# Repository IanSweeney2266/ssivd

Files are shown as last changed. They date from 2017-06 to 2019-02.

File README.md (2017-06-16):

# Small Scale Intelligent Vehicle Design platform (SSIVD)
Software and hardware documentation for creating an implementation of the Cal Poly SLO small-scale intelligent vehicle design platform

All original work is licensed under the MIT license, and all derivative work is licensed under the appropriate parent license 

If there are any concerns regarding licensing, get in touch and we will attempt to resolve it as soon as possible

#Statement of Disclaimer

Since this project is a result of a class assignment, it has been graded and accepted as fulfillment of the
course requirements. Acceptance does not imply technical accuracy or reliability. Any use of information
in this report is done at the risk of the user. These risks may include catastrophic failure of the device or
infringement of patent or copyright laws. California Polytechnic State University at San Luis Obispo and
its staff cannot be held liable for any use or misuse of the project.

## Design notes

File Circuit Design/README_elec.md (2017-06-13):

This folder contains the Eagle files for the SSIVD motherboard.

See the final design report for the full bill of materials.

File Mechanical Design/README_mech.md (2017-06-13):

This folder contains the solidworks files for the mechanical system of the SSIVD. 

Note that exact geometries of suspension components may vary, and the length of the steering linkage bar may need to be adjusted.

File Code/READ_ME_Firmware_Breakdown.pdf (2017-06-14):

# Firmware Breakdown

There are many files attached to the main Arduino loop, Teensy_Firmware. In this section we will go over which files you need to be aware of and which you can ignore.

IMU: (From a documented Library)

The BNO055 takes up quite a few files. Adafruit_BNO055.cpp, Adafruit_BNO055.h, Adafruit_Sensor.h, imumaths.h, matrix.h, structs.h, quarternion.h, vector.h, BNO.cpp, and BNO.h all have to do with the IMU. If you need to look into how the IMU is handled start with BNO.cpp and BNO.h as these are the files that incorporate all the rest.

Indicator LED: (User made files)

Fault_handler.cpp and fault_handler.h hold the functions we use to initialize and set the on-board LED. There's not too much here, although if you're looking to change the LED color check out our pre-made selection in fault_handler.h.

Throttle/Steering Input and URF Distance Sensor : (User made files)

All handling of the radio receiver's PWM input is handled through input_handler.cpp and input_handler.h. Here you will find the interrupt that catches the starting timestamp of the PWM and the handling of the calculated difference between that and the ending. We limit the throttle input from –500 to 500 and the servo input from –400 to 400. The URF sensor's initializing and polling functions are also handled here.

Servo Output: (User made files)

Sending a PWM pulse to the servo happens through output_handler.cpp and output_handler.h. The useful functions here are initServo and writeServo.

CAN Library: (From a documented Library)

FlexCAN.cpp, FlexCAN.h, and kinetis_flexcan.h provide a CAN library that allowed us to simply call functions to start the Teesny's CAN bus and to read and send the CAN messages. All CAN library support comes from these two files.

Motor Controller Interfacing: (User made files)

Building from the CAN library in FlexCAN.cpp, uLaren_CAN_Driver.cpp and uLaren_CAN_Driver.h have the heavy task of creating all the specific CAN functionality to use the motor controllers. Setting up their network, initializing them, setting the target velocity and much more is found in these files.

Laser Sensor (From a documented Library)

Adafruit_VL53L0X.cpp, Adafruit_VL53L0X.h, and the twenty other files that start with "vl53l0x" all provide support for the VL53L0X Laser Sensor. The only notable files are the Adafruit_VL53L0X.cpp and the Adafruit_VL53L0X.h. The other files support these two.

Main Loop Support (User made files)

As the system is right now, we have one file that supports the main loop, loop.h. This file contains the states the main loop is allowed to cycle through.

1.1.1 Teensy Main Loop Brief

There are two critical things to know that pertain to the main loop file Teensy_Firmware: the state transitions and the global variables used. We'll start with explaining the state transitions.

INITIALIZE_PERIPHERALS

In this state we initialize any sensors we wish to use. The indicator led gets set to white here. Once we're done here we move on to INITIALIZE_CONTROLLERS.

INITIALIZE_CONTROLLERS

This state is used specifically for the Maxon motor controllers. We start by resetting the nodes in case they were previously in a fault state. We continue by initializing the CAN network for every node (motor controller) on the network and going around one by one and initializing them to various modes and settings. The notable settings are changing to Profile Velocity Mode and turning the controller into the Switched-On state. The code in uLaren_CAN_Driver.cpp is well documented for all settings. Once initialized, the code moves on to the WAIT_FOR_ARM state.

WAIT_FOR_ARM

As the name implies, we wait for the user to arm the system and motor controllers by turning and holding the steering as far right as possible. This is indicated on the LED by transitioning to a yellow color. Once armed, we then transition to the LINK_COMMUNICATION state.

LINK_COMMUNICATION

Here we set each motor controller to the Operation Enabled state which is the final state and enables the motors to be "running". In this state the indicator LED becomes red. The initial velocity here is set to '0' which gives the motors holding power. This stage is rather complex and sometimes we need to try to rearm the controller. The code here handles this case and is quite impressive in its robustness. Once all motor controllers are armed, we go to either the RUNNING_NOMINALLY state or RUNNING_SIMULINK state depending on whether the defined variable SIMULINK is set to a '0' or '1' respectively.

RUNNING_NOMINALLY

This stage is where the loop will stay at until we encounter an error. This state starts by checking to see if any CAN messages can be processed. It then attempts to write a new value to the motor controllers if 20 milliseconds have gone by; if it hasn't then it moves on. We then check the voltage level of the motor controllers to regulate the battery level. We decided to set a minimum voltage level of 22V and if this level isn’t met the LED indicator changes to a purple color and shuts down all the motor controllers. In most cases we continue through the state and attempt to write to the servo if 10 milliseconds have gone by. In this state the indicator LED is green.

RUNNING_SIMULINK

This state is very similar to RUNNING_NOMINALLY. The difference is that instead of taking input directly from the radio receiver we send it to Simulink first and use the values that Simulink sends back. To implement this, we had to use the Raspberry Pi/Simulink as the SPI master while the Teensy was the receiver. We used a one-byte opcode to indicate to the Teensy which functionality the Raspberry Pi/Simulink is trying to use. To achieve this setting we incorporated a switch case using the one-byte prefixed opcode. Other than the switch case this state also incorporates all functionality that the RUNNING_NOMINALLY state has. Here the indicator LED is supposed to be cyan but it looks more white in reality.

INDICATE_AND_LOG_ERROR

WAIT_FOR_CLEAR

These states have yet to be implemented. They were developed in the prototype phase and serve as a base for future projects to use.

1.1.2 Teensy’s Pertinent Variables

SIMULINK: The SIMULINK defined variable is used to switch between the RUNNING_NOMINALLY functionality and the RUNNING SIMULINK functionality by writing a '0' or '1' respectively.

MC_VOLTAGE_THRESHOLD: This variable is used to set a minimum limit that the perceived voltage by the motor controllers must not dip below. This value is counted in 0.1V and we recommend not changing its value.

CANbus: The CANbus global variable is the key to all CAN communication. Key functions regarding this variable are specified in FlexCAN.h.

Next_state: This crucial global variable is how we interpret which state we are currently in.

All data and output variables are self-explanatory and are meant to be apparent in their meaning.

Timing variables are used to control how often we exercise certain functionality. As an example, we use the motor's timing variables to write approximately 50 times per second.

PRINT: Located in uLaren_CAN_Driver.h, if set to a '1' many items will be printed in the serial port and is quite helpful for debugging purposes.

SCALE_FACTOR: Be careful with this defined variable as it controls the factor we scale the throttle by. For normal use we advise not going above 2 to maintain similitude. The motors however are capable of going much higher (up to 8 is theoretically possible but is very strongly advised against and could destroy the motors).

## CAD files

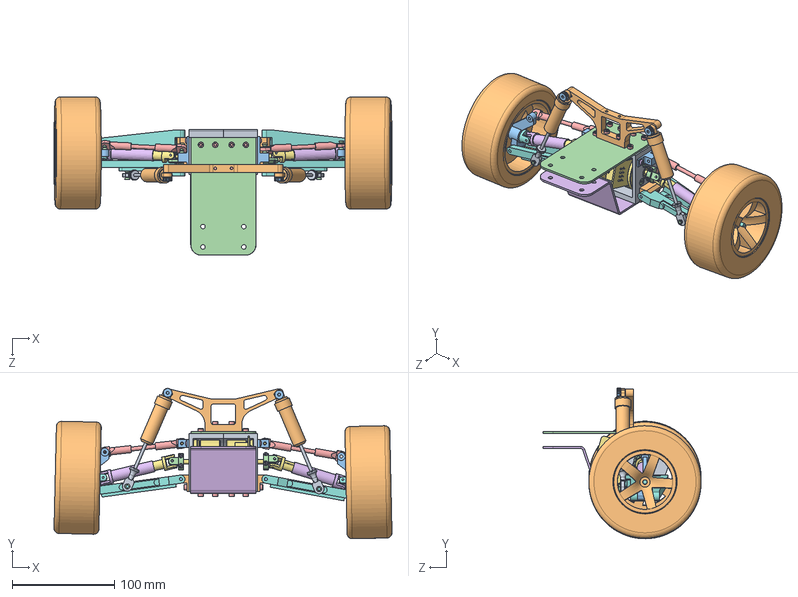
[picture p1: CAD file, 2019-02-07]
Mechanical Design/Parts and Assemblies/Custom Rear.SLDASM
330.9 x 147.4 x 155.0 mm
Rear drivemount_R3
Rear A Pivot x 2
Rear Turnbucklemount x 2
Shaft Coupler - SideA x 2
Shaft Coupler - SideB x 2
M2 - 10MM - Socket x 4
MaxonMotor x 2
U Joint A - Wheel_Rear x 2
U Joint Ball x 4
Wheel x 2
Suspension Mount_Rear x 2
Turnbuckle Ball Spacer x 6
Turnbuckle Bar_REAR x 2
U Joint A - Outer Yoke_Rear x 2
U Joint B - Inner Yoke_Rear x 2
Suspension Plate_R
Suspension Inner_Rear x 2
Suspension Outer_Rear x 2
A-Arm Dowel Pin x 2
M3-4MM -Flat x 6
M3 - 6MM - Socket x 18
M3 - 5MM - Rounded x 4
M3 - 14MM - Rounded x 2
Suspension Plate_L
Rear drivemount_L2
Suspension Mount Rear
M4 - 5MM - Shoulder x 2
Chassis Mount Rear_top
M3 - 12MM - Socket x 2
Chassis Mount RB Sheet Metal

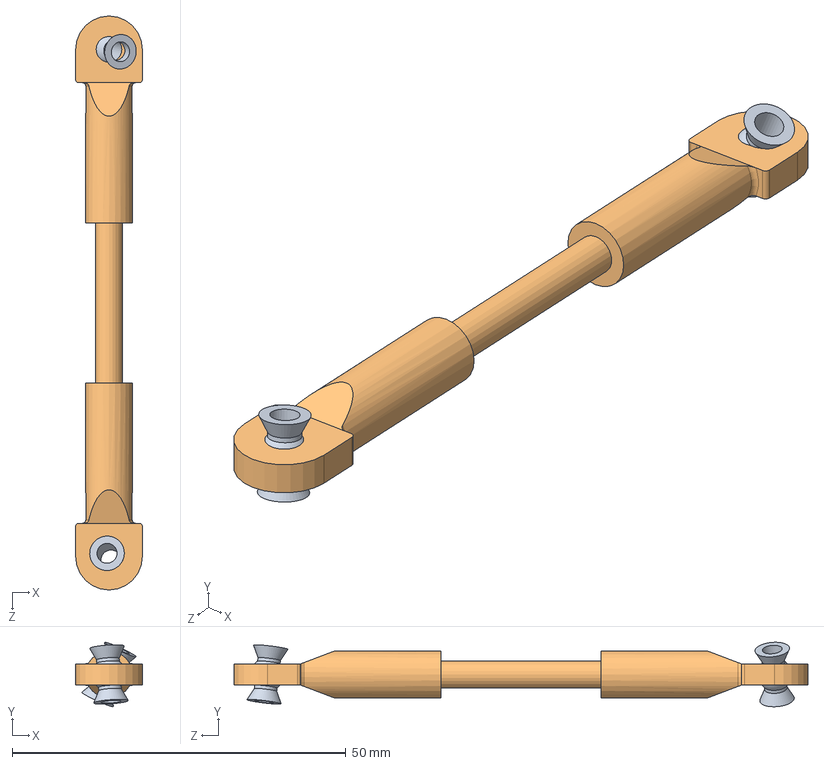
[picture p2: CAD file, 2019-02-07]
Mechanical Design/Parts and Assemblies/Stock Parts/Fore/Steering/Steering TurnbuckleAssy_fore.SLDASM
10.0 x 9.68 x 86.0 mm
Turnbuckle Ball Spacer x 2
Steering turnbuckle Bar_fore

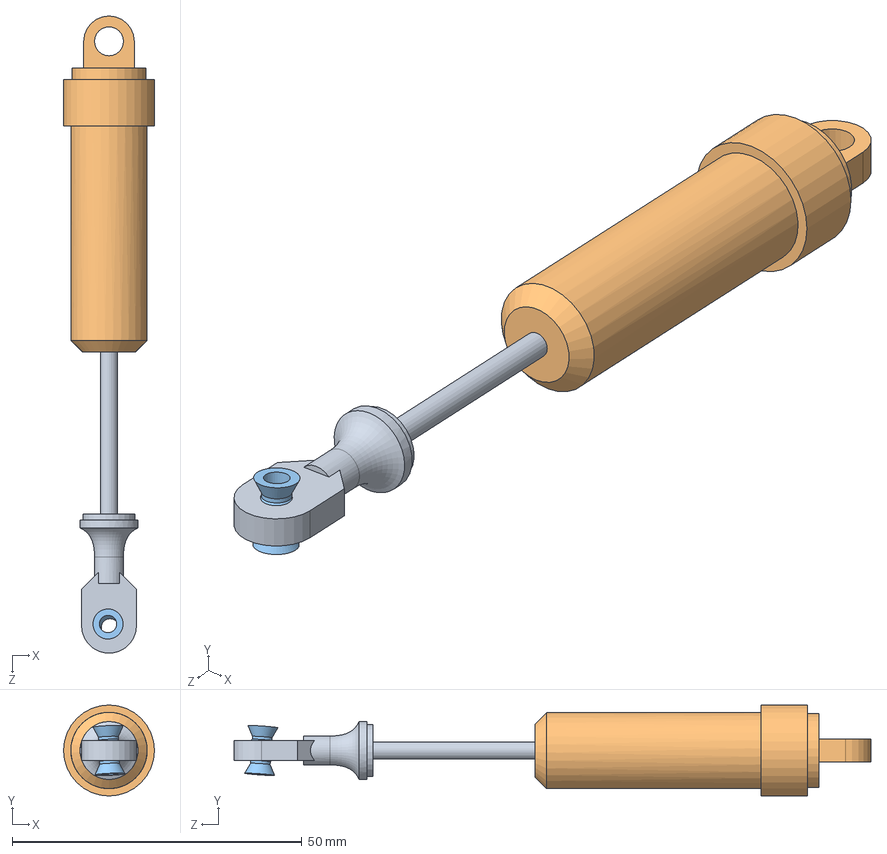
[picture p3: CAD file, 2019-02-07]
Mechanical Design/Parts and Assemblies/Stock Parts/Rear/Suspension_Rear.SLDASM
15.7 x 15.7 x 110.0 mm
Suspension Inner_Rear
Suspension Outer_Rear
Turnbuckle Ball Spacer

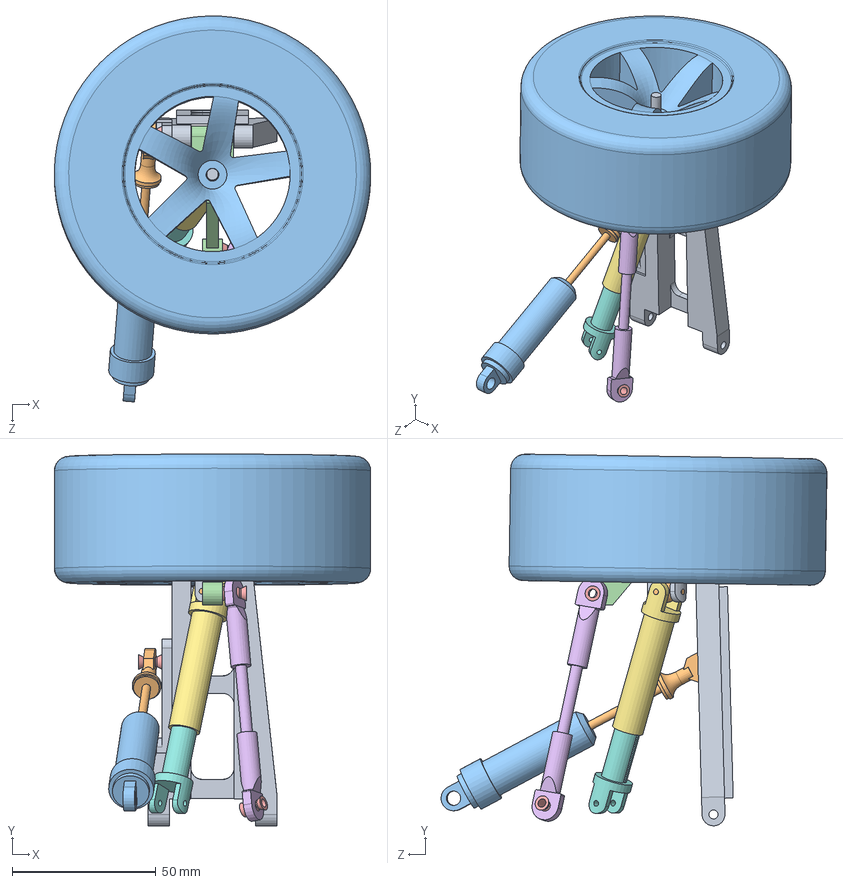
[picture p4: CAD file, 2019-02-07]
Mechanical Design/Parts and Assemblies/Stock Parts/Right Rear Assy.SLDASM
110.0 x 129.2 x 134.2 mm
U Joint A - Wheel_Rear
U Joint Ball
Wheel
Suspension Mount_Rear
Turnbuckle Ball Spacer x 3
Turnbuckle Bar_REAR
U Joint A - Outer Yoke_Rear
U Joint B - Inner Yoke_Rear
Suspension Plate_R
Suspension Inner_Rear
Suspension Outer_Rear

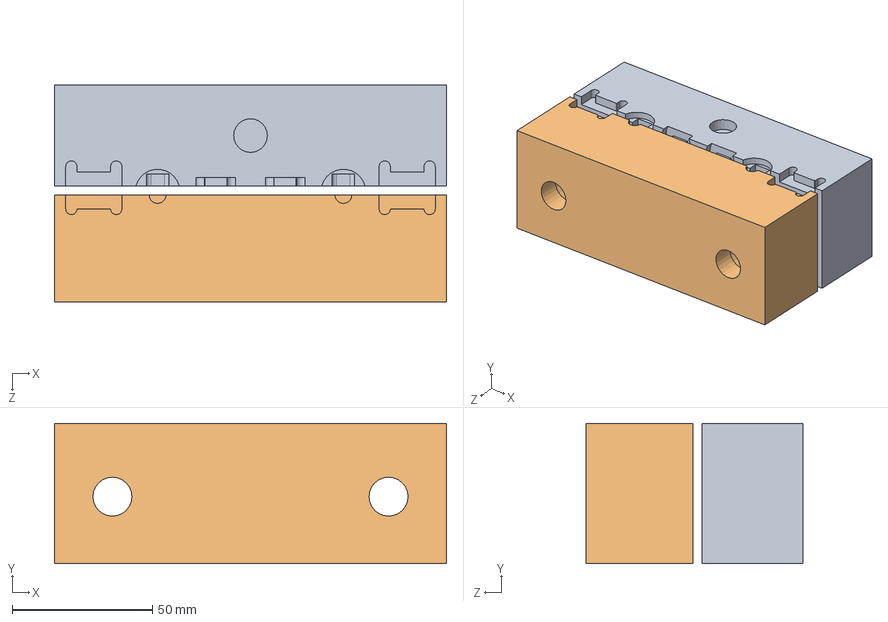
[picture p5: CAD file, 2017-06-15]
Mechanical Design/Automation/cnc/Soft Jaw Cutting Assy.SLDASM
139.7 x 50.0 x 77.3 mm
softjawA
softjawB

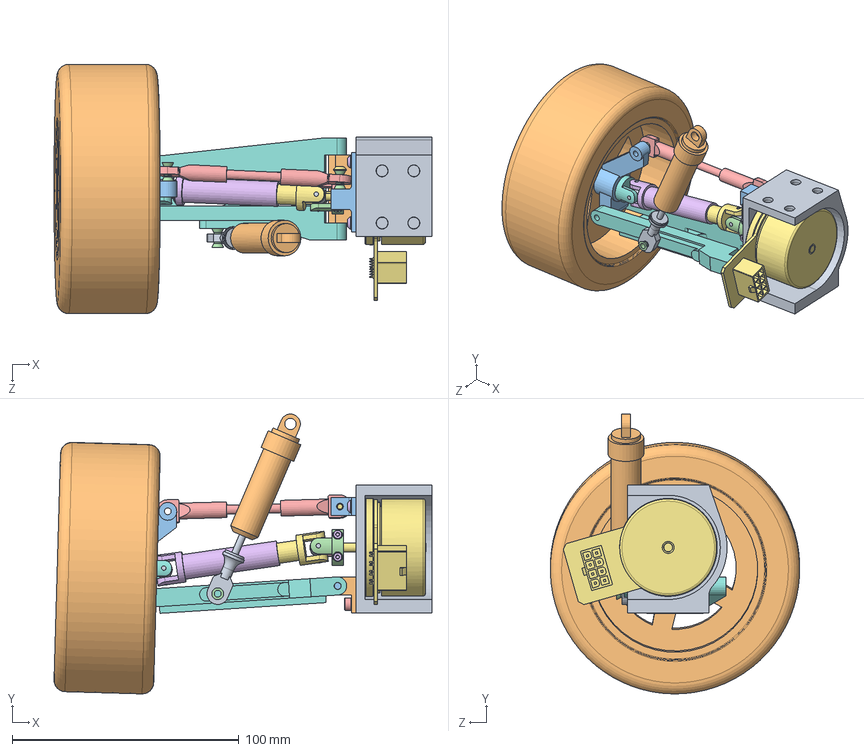
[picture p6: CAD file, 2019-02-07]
Mechanical Design/Parts and Assemblies/Custom Rear_R.SLDASM
166.7 x 123.4 x 109.9 mm
Rear drivemount_R3
Rear A Pivot
Rear Turnbucklemount
Shaft Coupler - SideA
Shaft Coupler - SideB
M2 - 10MM - Socket x 2
MaxonMotor
U Joint A - Wheel_Rear
U Joint Ball x 2
Wheel
Suspension Mount_Rear
Turnbuckle Ball Spacer x 3
Turnbuckle Bar_REAR
U Joint A - Outer Yoke_Rear
U Joint B - Inner Yoke_Rear
Suspension Plate_R
Suspension Inner_Rear
Suspension Outer_Rear
A-Arm Dowel Pin
M3-4MM -Flat x 3
M3 - 6MM - Socket x 2
M3 - 5MM - Rounded x 2
M3 - 14MM - Rounded

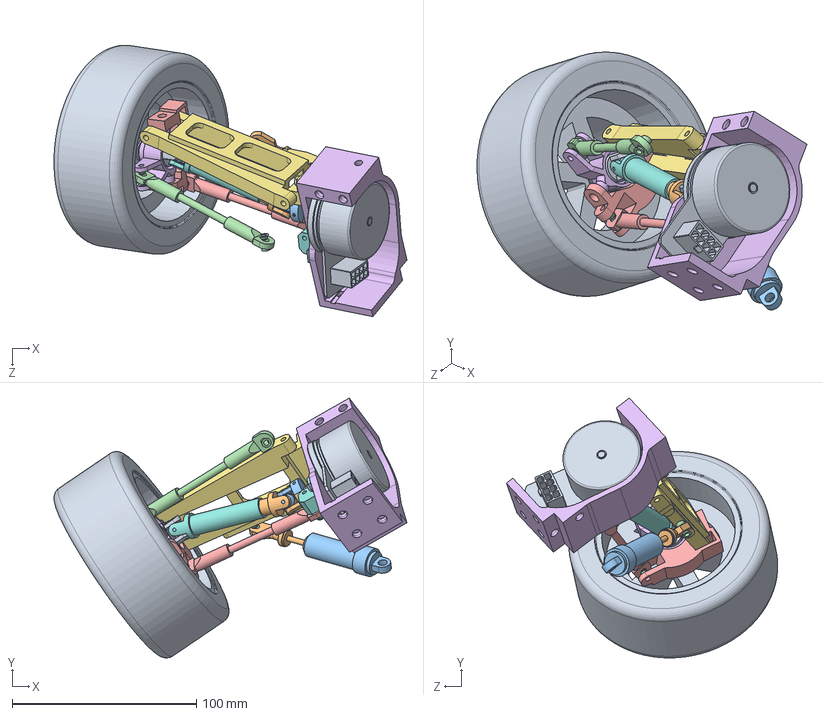
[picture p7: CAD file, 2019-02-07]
Mechanical Design/Parts and Assemblies/Stock Parts/Front Right Assy.SLDASM
191.4 x 140.9 x 147.1 mm
Wheel
Suspension Inner_fore
Suspension Outer_fore
Turnbuckle Ball Spacer x 5
Suspension Mount Fore-Right
SteeringControlArm-Right
Suspension Plate_R
U Joint A - Outer Yoke_fore
U Joint A - Wheel_fore
U Joint B - Inner Yoke_fore
U Joint Ball x 2
Steering turnbuckle Bar_fore
Turnbuckle Bar_fore
Front Drivemount_R2
Front A Pivot
Front Turnbucklemount
MaxonMotor
Shaft Coupler - SideA
Shaft Coupler - SideB
M2 - 10MM - Socket x 2
M3-4MM -Flat x 3
M3 - 5MM - Rounded x 2
M3 - 12MM - Socket x 2
M3 - 14MM - Rounded

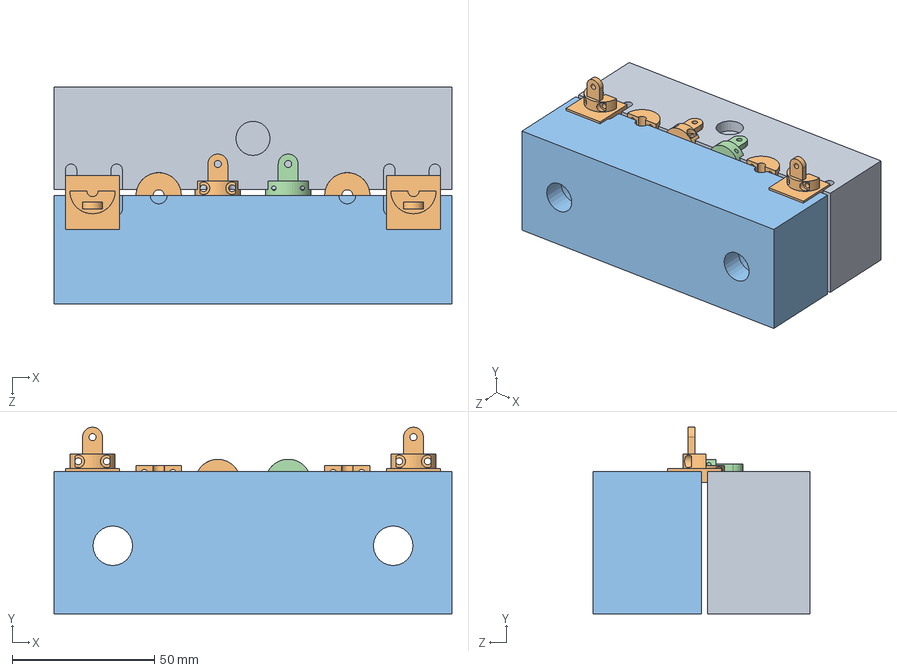
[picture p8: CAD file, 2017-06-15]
Mechanical Design/Automation/cnc/softjawfit.SLDASM
139.7 x 65.5 x 76.1 mm
softjawA
Shaft Coupler - SideA x 5
softjawB
Shaft Coupler - SideB

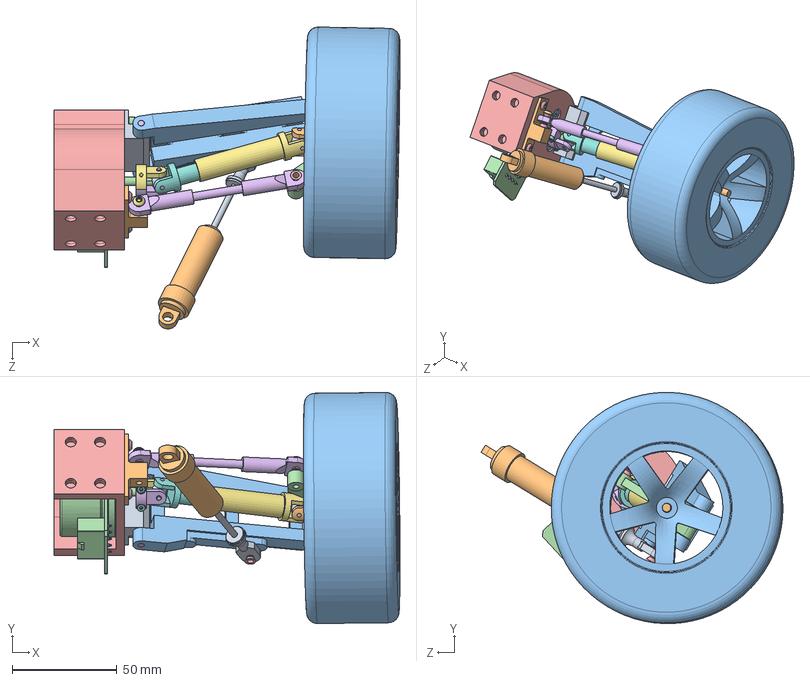
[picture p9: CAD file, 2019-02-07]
Mechanical Design/Parts and Assemblies/Custom Rear_L.SLDASM
165.1 x 110.3 x 144.1 mm
U Joint Ball x 2
U Joint A - Wheel_Rear
Wheel
Suspension Mount_Rear
Turnbuckle Ball Spacer x 3
Turnbuckle Bar_REAR
U Joint A - Outer Yoke_Rear
U Joint B - Inner Yoke_Rear
Suspension Inner_Rear
Suspension Outer_Rear
Suspension Plate_L
MaxonMotor
Rear drivemount_L2
Shaft Coupler - SideA
Shaft Coupler - SideB
M2 - 10MM - Socket x 2
Rear A Pivot
Rear Turnbucklemount
M3-4MM -Flat x 3
M3 - 6MM - Socket x 2
M3 - 5MM - Rounded x 2
A-Arm Dowel Pin
M3 - 14MM - Rounded

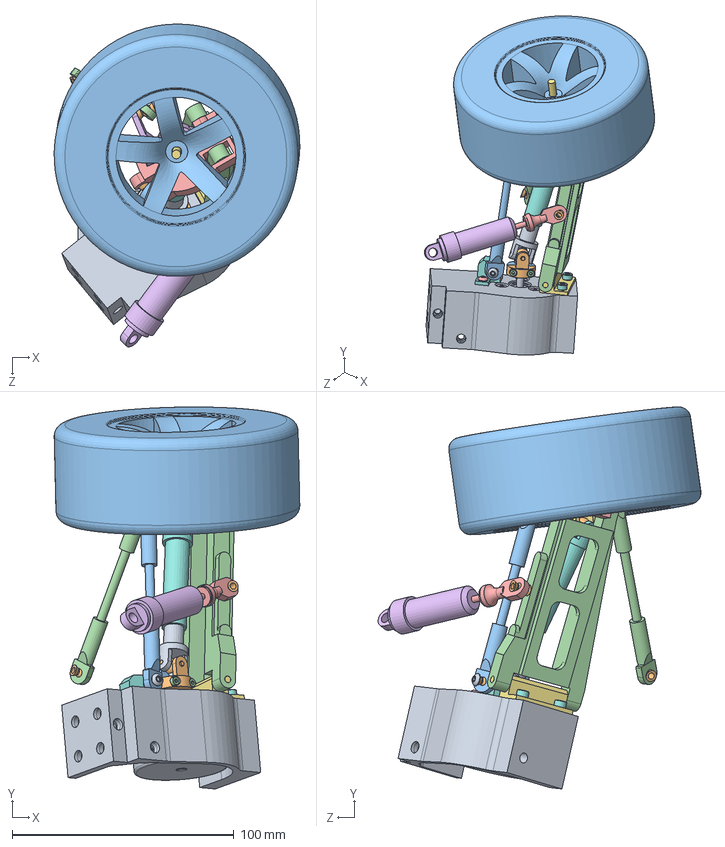
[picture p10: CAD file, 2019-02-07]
Mechanical Design/Parts and Assemblies/Stock Parts/Front Left Assy.SLDASM
110.7 x 172.2 x 145.5 mm
Front Drivemount_L2
U Joint Ball x 2
Wheel
Suspension Plate_L
Suspension Mount Fore-Left
SteeringControlArm-Left
U Joint A - Wheel_fore
U Joint A - Outer Yoke_Rear
U Joint B - Inner Yoke_Rear
Turnbuckle Ball Spacer x 5
Turnbuckle Bar_fore
Steering turnbuckle Bar_fore
Suspension Inner_fore
Suspension Outer_fore
Front A Pivot
Front Turnbucklemount
MaxonMotor
Shaft Coupler - SideA
Shaft Coupler - SideB
M2 - 10MM - Socket x 2
M3 - 5MM - Rounded x 2
M3-4MM -Flat x 3
A-Arm Dowel Pin
M3 - 12MM - Socket x 2
M3 - 14MM - Rounded

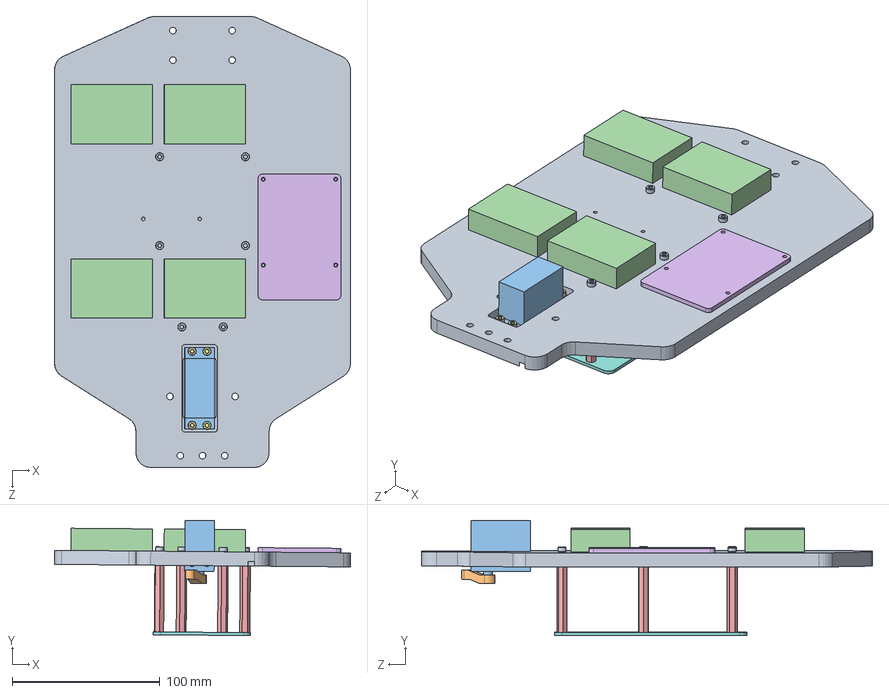
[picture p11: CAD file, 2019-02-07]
Mechanical Design/Parts and Assemblies/Chassis.SLDASM
200.1 x 77.9 x 304.8 mm
Chassis_New
Servo Horn
Steering Servo
50-5 module x 4
45 MM M3 Standoff x 6
RPi
M3 - 6MM - Socket x 4
Battery shelf
M3 - 12MM - Socket x 6

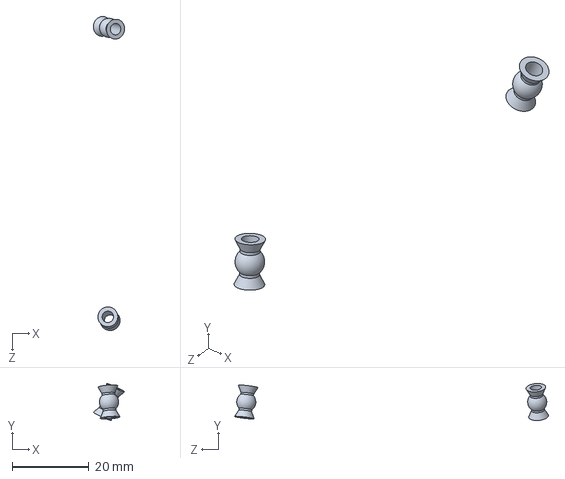
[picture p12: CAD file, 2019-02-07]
Mechanical Design/Parts and Assemblies/Stock Parts/Rear/TurnbuckleAssy_Rear.SLDASM
8.15 x 9.68 x 82.0 mm
Turnbuckle Ball Spacer x 2

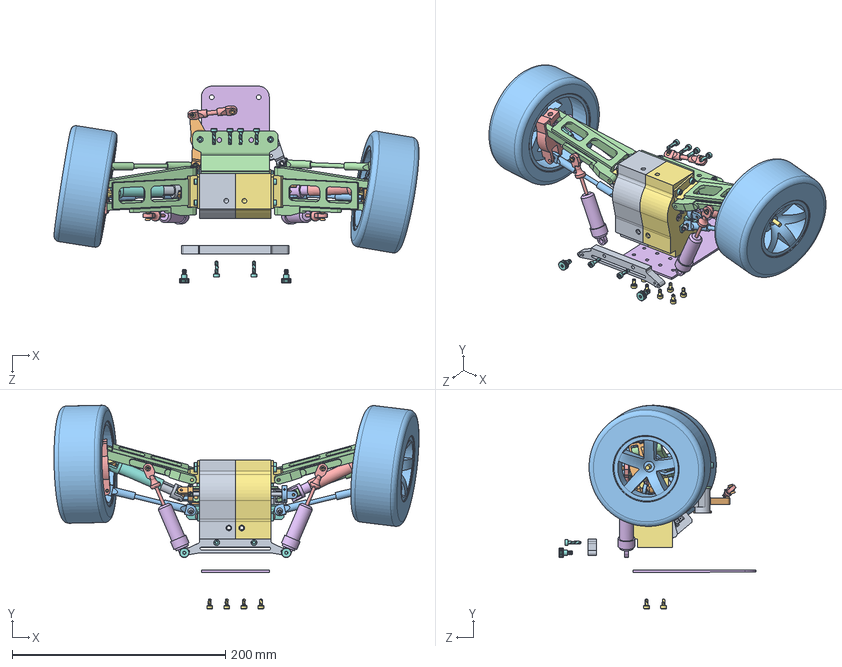
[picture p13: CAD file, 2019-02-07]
Mechanical Design/Parts and Assemblies/Custom Front.SLDASM
342.1 x 190.8 x 184.5 mm
Front Drivemount_L2
U Joint Ball x 4
Wheel x 2
Suspension Plate_L
Suspension Mount Fore-Left
SteeringControlArm-Left
U Joint A - Wheel_fore x 2
U Joint A - Outer Yoke_Rear
U Joint B - Inner Yoke_Rear
Turnbuckle Ball Spacer x 12
Turnbuckle Bar_fore x 2
Steering turnbuckle Bar_fore x 2
Suspension Inner_fore x 2
Suspension Outer_fore x 2
Front A Pivot x 2
Front Turnbucklemount x 2
MaxonMotor x 2
Shaft Coupler - SideA x 2
Shaft Coupler - SideB x 2
M2 - 10MM - Socket x 4
M3 - 5MM - Rounded x 4
M3-4MM -Flat x 6
A-Arm Dowel Pin
M3 - 12MM - Socket x 12
M3 - 14MM - Rounded x 2
Suspension Mount Fore-Right
SteeringControlArm-Right
Suspension Plate_R
U Joint A - Outer Yoke_fore
U Joint B - Inner Yoke_fore
Front Drivemount_R2
Steering Post Dowel x 2
LinkagePost
LinkagePostwspring
steering link
Chassis Mount FB Sheet Metal
Linkage Turnbuckle Bar_fore
Chassis Mount front_top
M3 - 6MM - Socket x 8
M4 - 5MM - Shoulder x 2
Front suspension mount rev 2

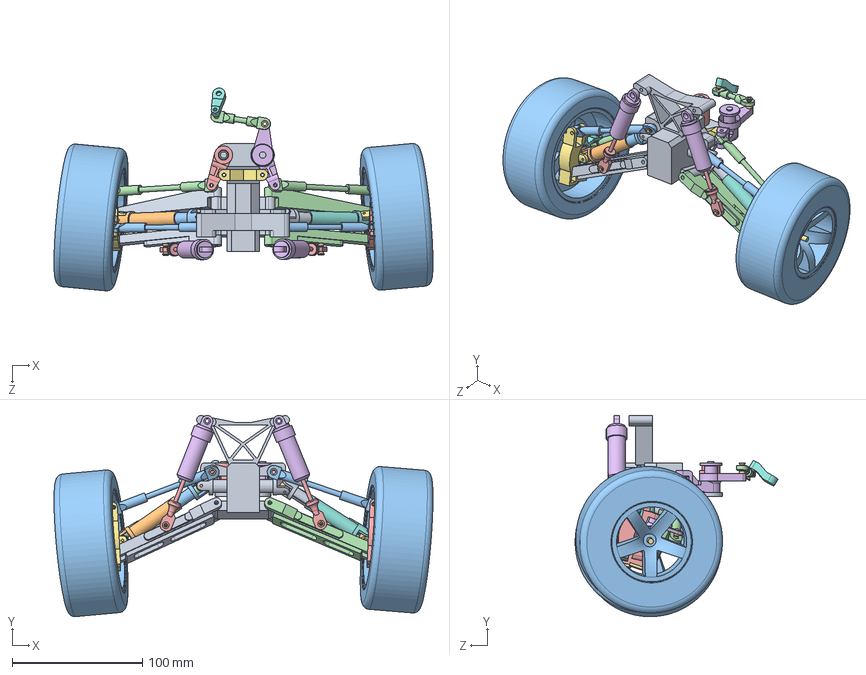
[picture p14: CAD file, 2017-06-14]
Mechanical Design/Parts and Assemblies/Stock Parts/Front Stock.SLDASM
290.9 x 154.5 x 155.7 mm
Center Fixture_fore
U Joint Ball x 4
Wheel x 2
Suspension Plate_L
Suspension Mount Fore-Left
SteeringControlArm-Left
U Joint A - Wheel_fore x 2
U Joint A - Outer Yoke_Rear
U Joint B - Inner Yoke_Rear
Turnbuckle Ball Spacer x 12
Turnbuckle Bar_fore x 2
Steering turnbuckle Bar_fore x 2
Suspension Inner_fore x 2
Suspension Outer_fore x 2
Suspension Mount Fore-Right
SteeringControlArm-Right
Suspension Plate_R
U Joint A - Outer Yoke_fore
U Joint B - Inner Yoke_fore
Linkage Turnbuckle Bar_fore
LinkagePost
LinkagePostwspring
Post Linkage
Servo Horn
STD U joint x 2

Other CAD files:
Mechanical Design/Parts and Assemblies/Stock Parts/Fore/Slip Yoke_fore.SLDASM
Mechanical Design/Parts and Assemblies/Stock Parts/Front Stock (Jay Miley's conflicted copy 2017-01-17).SLDASM
Mechanical Design/Parts and Assemblies/Stock Parts/Fore/Steering/Linkage TurnbuckleAssy_fore.SLDASM
Mechanical Design/Parts and Assemblies/Stock Parts/Rear_Stock.SLDASM
Mechanical Design/Automation/Laser Cut/Grant_Acrylic.dwg
Mechanical Design/Automation/Laser Cut/TemplateChassis.dwg
Mechanical Design/Automation/Water Jet/Chassis (Nylon)/Chassis(in).DXF
Mechanical Design/Automation/Water Jet/Chassis Mounts (Sheet Metal)/Chassis Mounts.dxf
Mechanical Design/Automation/Water Jet/Chassis Mounts (Sheet Metal)/FB(in).DXF
Mechanical Design/Automation/Water Jet/Chassis Mounts (Sheet Metal)/FT(in).DXF
Mechanical Design/Automation/Water Jet/Chassis Mounts (Sheet Metal)/RB(in).DXF
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

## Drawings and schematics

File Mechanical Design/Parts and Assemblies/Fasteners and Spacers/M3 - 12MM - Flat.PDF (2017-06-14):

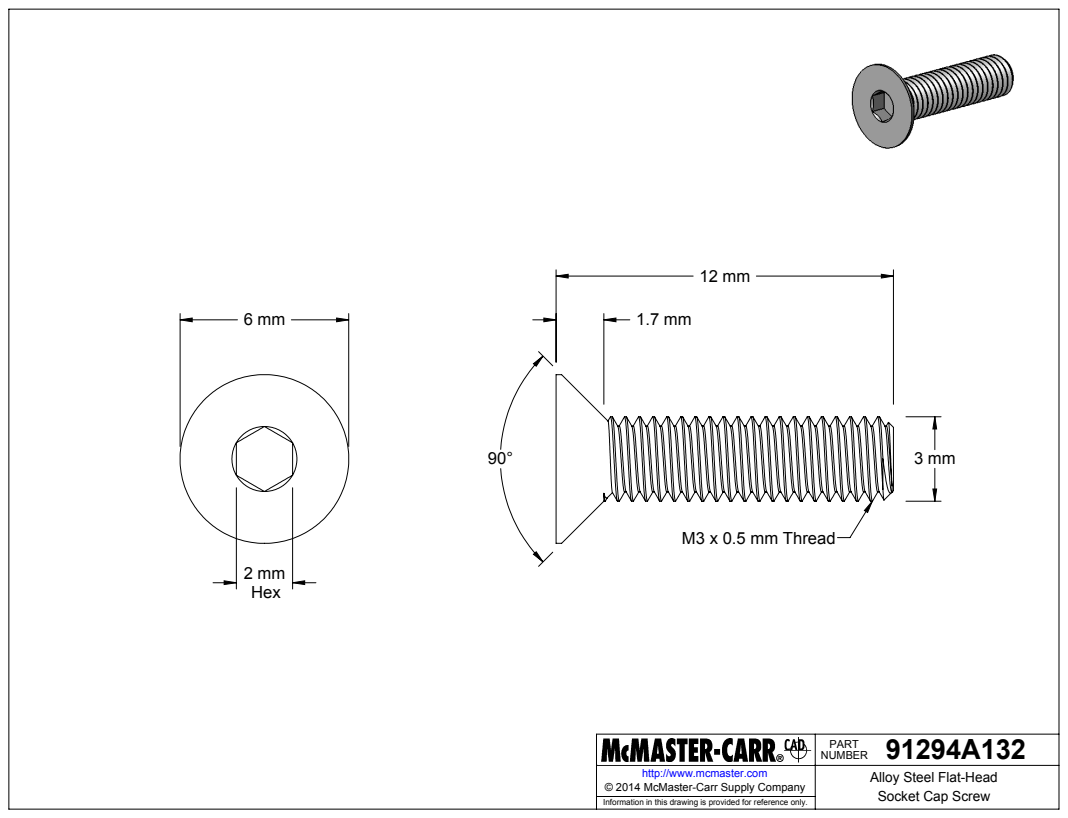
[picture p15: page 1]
M3 x 0.5 mm Thread

91294A132 PART NUMBER

http://www.mcmaster.com | Alloy Steel Flat-Head Socket Cap Screw © 2014 McMaster-Carr Supply Company

Information in this drawing is provided for reference only.

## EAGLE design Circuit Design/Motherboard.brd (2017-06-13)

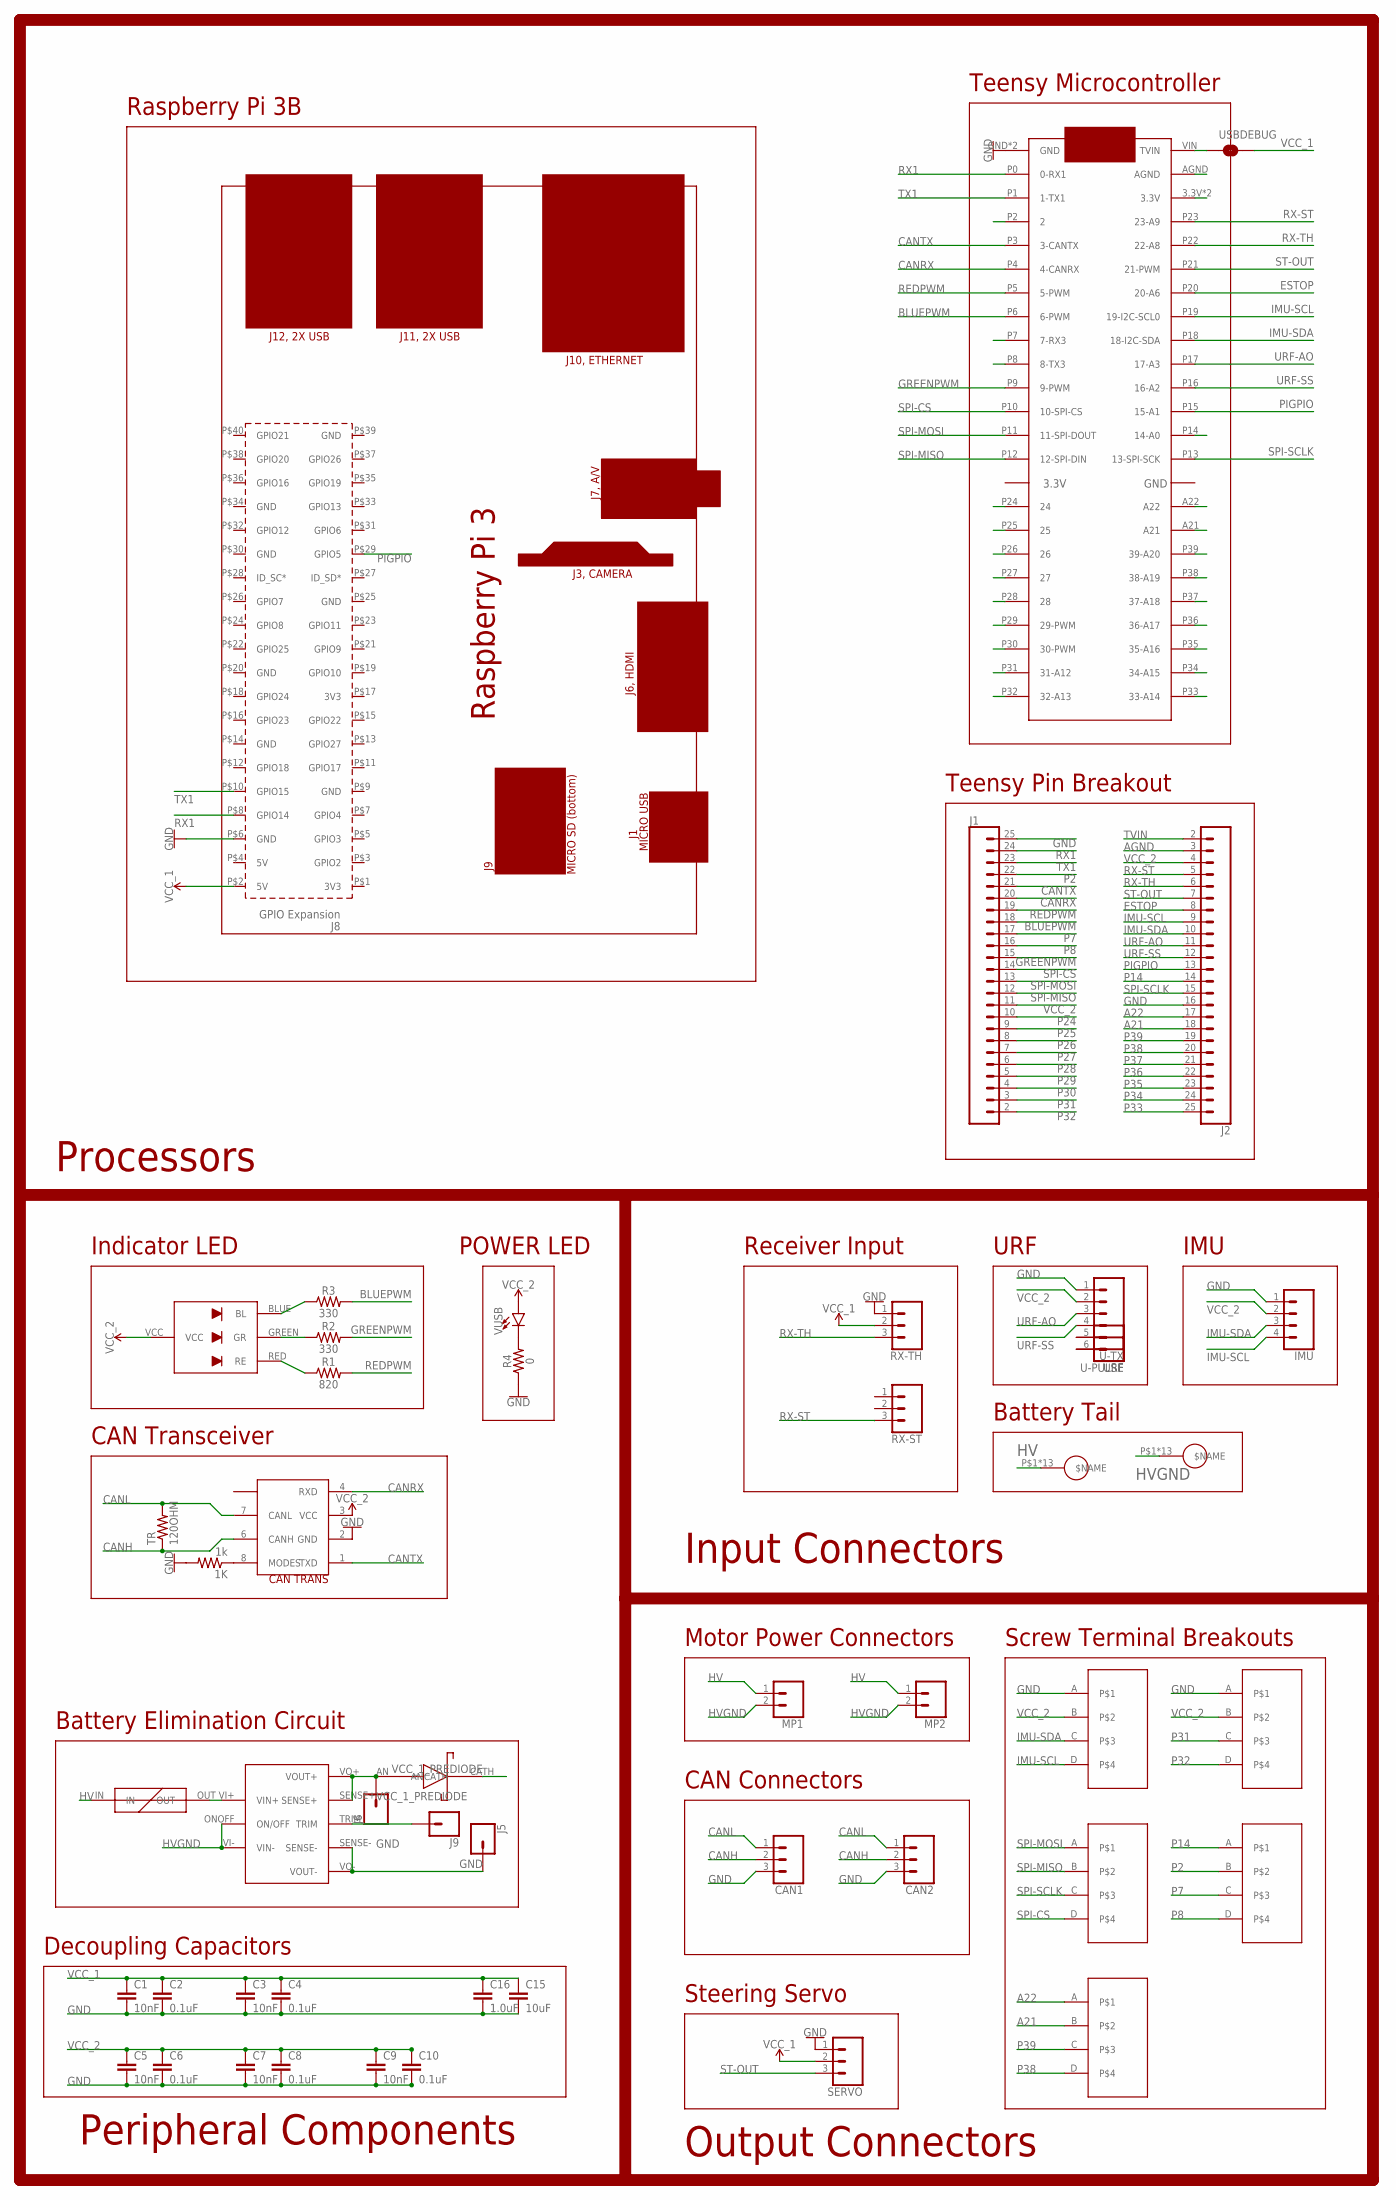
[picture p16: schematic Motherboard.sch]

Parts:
1K: 1k; R0603
C1, C3, C5, C7, C9: 10nF; 0603
C2, C4, C6, C8, C10: 0.1uF; 0603
C15: 10uF; 1206
C16: 1.0uF; 1206
CAN1, CAN2: CONN_03SCREW; SCREWTERMINAL-3.5MM-3
DAC/ADC: SCREWTERM
HV+: WIREPAD
HV-: WIREPAD
I2C: SCREWTERM
IMU: CONN_041X04_NO_SILK; 1X04_NO_SILK
J1, J2: CONN_24; 1X24
J5, J6, J9: CONN_01PTH_NO_SILK_YES_STOP; 1X01_NO_SILK
MP1, MP2: CONN_023.5MM; SCREWTERMINAL-3.5MM-2
PCB1: RPI3
PWM: SCREWTERM
R1: 820; 0603
R2, R3: 330; 0603
R4: 0; 0603
RPI-SPI: SCREWTERM
RX-ST: CONN_03; 1X03
RX-TH: CONN_03; 1X03
SERVO: CONN_03; 1X03
TEENS: TEENSY3.6
TR: 120OHM; R0603
U$1: CREERGB
U$2: CAN-TRANS; SO08
U$4: BEC
U$5: LITTLEFUSE
U$6: SCHOTTKY; 2114
U-PULSE: CONN_01PTH_NO_SILK_YES_STOP; 1X01_NO_SILK
U-TX: CONN_01PTH_NO_SILK_YES_STOP; 1X01_NO_SILK
UART: SCREWTERM
URF: CONN_06NO_SILK_FEMALE_PTH; 1X06_NO_SILK
USBDEBUG: JUMPER-SMT_2_NO_NO-SILK; SMT-JUMPER_2_NO_NO-SILK
VUSB: LED0603; LED-0603

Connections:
A21: DAC/ADC.B, J2.18, TEENS.A21
A22: DAC/ADC.A, J2.17, TEENS.A22
AGND: J2.3, TEENS.AGND
BLUEPWM: J1.18, R3.2, TEENS.P6 (6-PWM)
CANH: CAN1.2, CAN2.2, TR.1, U$2.6 (CANH)
CANL: CAN1.1, CAN2.1, TR.2, U$2.7 (CANL)
CANRX: J1.20, TEENS.P4 (4-CANRX), U$2.4 (RXD)
CANTX: J1.21, TEENS.P3 (3-CANTX), U$2.1 (TXD)
ESTOP: J2.8, TEENS.P20 (20-A6)
FUSEDHV: U$4.VI+ (VIN+), U$5.OUT
GND: 1K.2, C1.2, C2.2, C3.2, C4.2, C5.2, C6.2, C7.2, C8.2, C9.2, C10.2, C15.2, C16.2, CAN1.3, CAN2.3, I2C.A, IMU.1, J1.25, J2.16, J5.1, PCB1.P$6 (GND), R4.1, RX-TH.1, SERVO.1, TEENS.GND, TEENS.GND2 (GND), U$2.2 (GND), U$4.SENSE-, U$4.VO- (VOUT-), UART.A, URF.1
GREENPWM: J1.15, R2.2, TEENS.P9 (9-PWM)
HV: HV+.P$1, HV+.P$2, HV+.P$3, HV+.P$4, HV+.P$5, HV+.P$6, HV+.P$7, HV+.P$8, HV+.P$9, HV+.P$10, HV+.P$11, HV+.P$12, HV+.P$13, MP1.1, MP2.1, U$5.IN
HVGND: HV-.P$1, HV-.P$2, HV-.P$3, HV-.P$4, HV-.P$5, HV-.P$6, HV-.P$7, HV-.P$8, HV-.P$9, HV-.P$10, HV-.P$11, HV-.P$12, HV-.P$13, MP1.2, MP2.2, U$4.ONOFF (ON/OFF), U$4.VI- (VIN-)
IMU-SCL: I2C.D, IMU.4, J2.9, TEENS.P19 (19-I2C-SCL0)
IMU-SDA: I2C.C, IMU.3, J2.10, TEENS.P18 (18-I2C-SDA)
unnamed: U-PULSE.1, URF.6
unnamed: U-TX.1, URF.5
unnamed: 1K.1, U$2.8 (MODES)
unnamed: R4.2, VUSB.C
unnamed: J9.1, U$4.TRIM
unnamed: R1.1, U$1.RED (RE)
unnamed: R2.1, U$1.GREEN (GR)
unnamed: R3.1, U$1.BLUE (BL)
P2: J1.22, PWM.B, TEENS.P2 (2)
P7: J1.17, PWM.C, TEENS.P7 (7-RX3)
P8: J1.16, PWM.D, TEENS.P8 (8-TX3)
P14: J2.14, PWM.A, TEENS.P14 (14-A0)
P24: J1.10, TEENS.P24 (24)
P25: J1.9, TEENS.P25 (25)
P26: J1.8, TEENS.P26 (26)
P27: J1.7, TEENS.P27 (27)
P28: J1.6, TEENS.P28 (28)
P29: J1.5, TEENS.P29 (29-PWM)
P30: J1.4, TEENS.P30 (30-PWM)
P31: J1.3, TEENS.P31 (31-A12), UART.C
P32: J1.2, TEENS.P32 (32-A13), UART.D
P33: J2.25, TEENS.P33 (33-A14)
P34: J2.24, TEENS.P34 (34-A15)
P35: J2.23, TEENS.P35 (35-A16)
P36: J2.22, TEENS.P36 (36-A17)
P37: J2.21, TEENS.P37 (37-A18)
P38: DAC/ADC.D, J2.20, TEENS.P38 (38-A19)
P39: DAC/ADC.C, J2.19, TEENS.P39 (39-A20)
PIGPIO: J2.13, PCB1.P$29 (GPIO5), TEENS.P15 (15-A1)
REDPWM: J1.19, R1.2, TEENS.P5 (5-PWM)
RX1: J1.24, PCB1.P$8 (GPIO14), TEENS.P0 (0-RX1)
RX-ST: J2.5, RX-ST.3, TEENS.P23 (23-A9)
RX-TH: J2.6, RX-TH.3, TEENS.P22 (22-A8)
SPI-CS: J1.14, RPI-SPI.D, TEENS.P10 (10-SPI-CS)
SPI-MISO: J1.12, RPI-SPI.B, TEENS.P12 (12-SPI-DIN)
SPI-MOSI: J1.13, RPI-SPI.A, TEENS.P11 (11-SPI-DOUT)
SPI-SCLK: J2.15, RPI-SPI.C, TEENS.P13 (13-SPI-SCK)
ST-OUT: J2.7, SERVO.3, TEENS.P21 (21-PWM)
TVIN: J2.2, TEENS.VIN (TVIN), USBDEBUG.1
TX1: J1.23, PCB1.P$10 (GPIO15), TEENS.P1 (1-TX1)
URF-AO: J2.11, TEENS.P17 (17-A3), URF.3
URF-SS: J2.12, TEENS.P16 (16-A2), URF.4
VCC_1: C1.1, C2.1, C3.1, C4.1, C15.1, C16.1, PCB1.P$2 (5V), RX-TH.2, SERVO.2, U$6.CATH, USBDEBUG.2
VCC_1_PREDIODE: J6.1, U$4.SENSE+, U$4.VO+ (VOUT+), U$6.AN
VCC_2: C5.1, C6.1, C7.1, C8.1, C9.1, C10.1, I2C.B, IMU.2, J1.11, J2.4, TEENS.3.3V, TEENS.3.3V2 (3.3V), U$1.VCC, U$2.3 (VCC), UART.B, URF.2, VUSB.A

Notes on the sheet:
Processors
Input Connectors
Output Connectors
Peripheral Components
Teensy Pin Breakout
Teensy Microcontroller
Raspberry Pi 3B
CAN Transceiver
Indicator LED
Motor Power Connectors
CAN Connectors
Steering Servo
Receiver Input
URF
IMU
Battery Tail
Battery Elimination Circuit
Screw Terminal Breakouts
Decoupling Capacitors
POWER LED

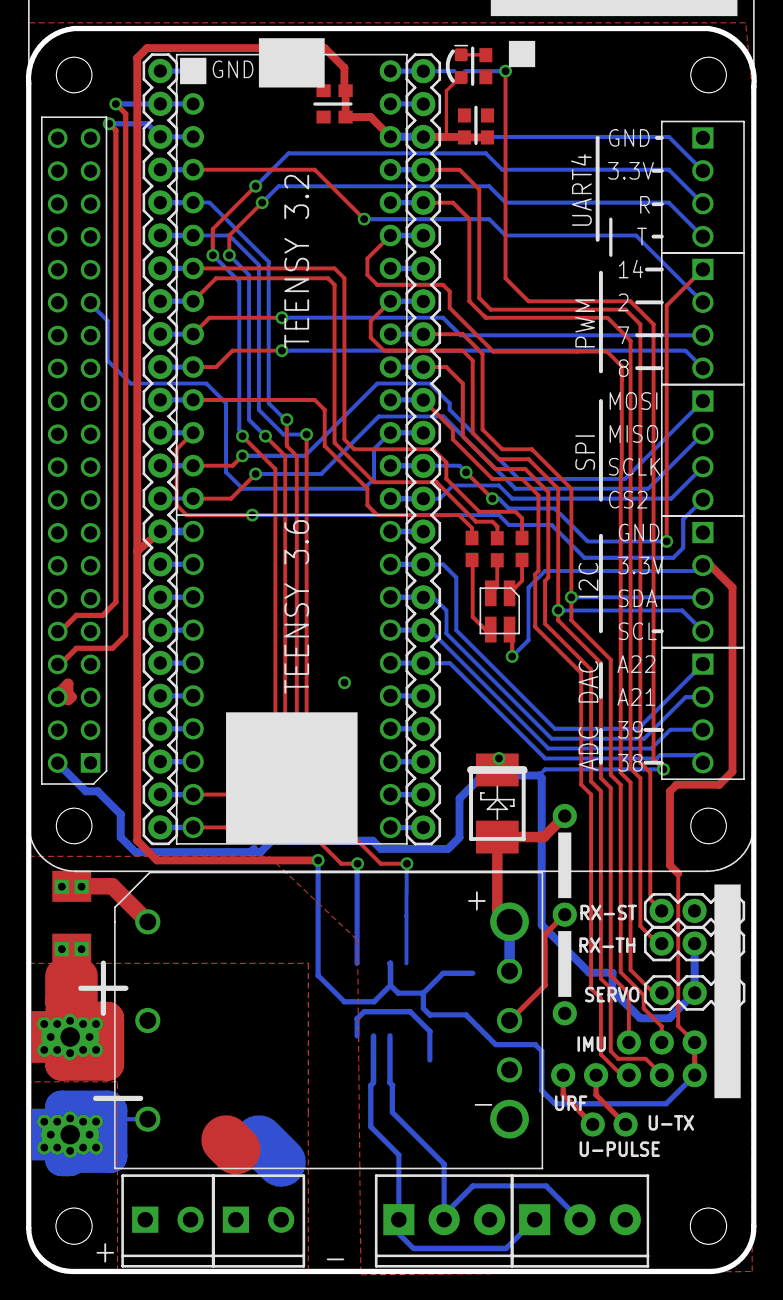
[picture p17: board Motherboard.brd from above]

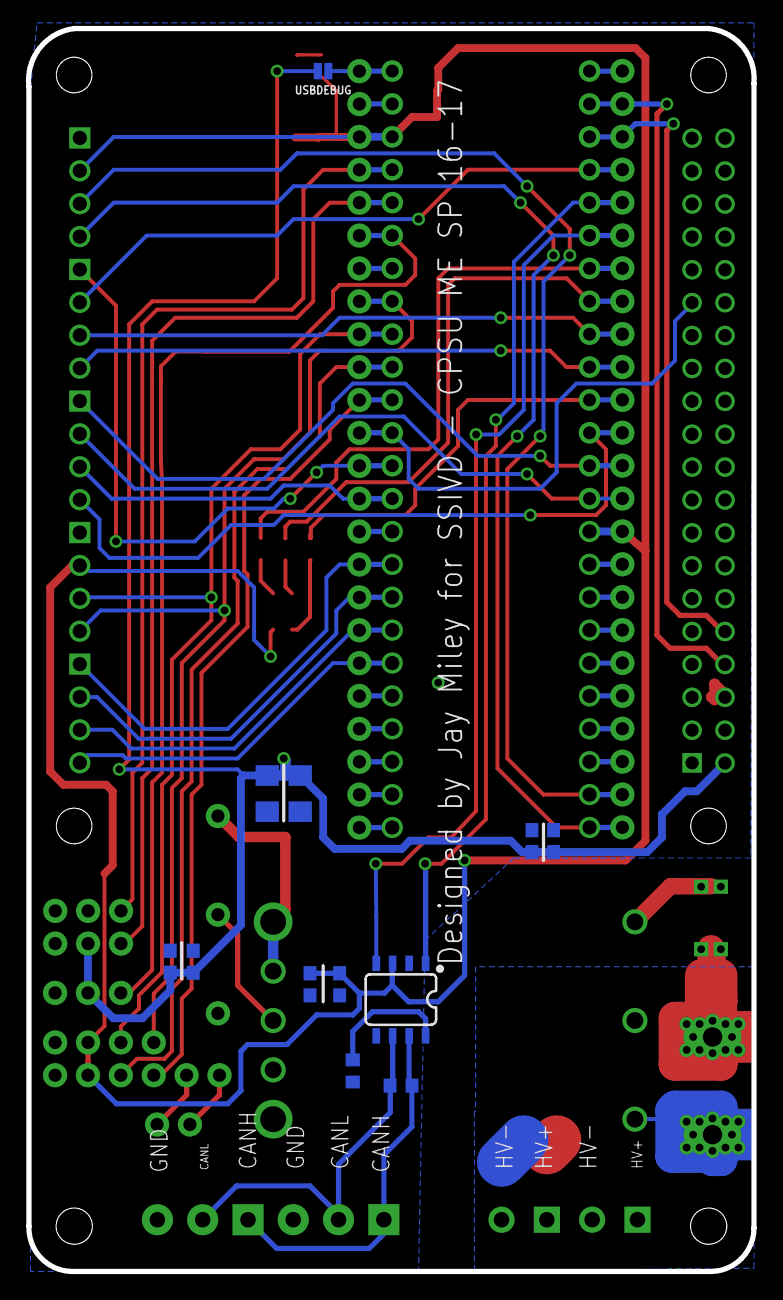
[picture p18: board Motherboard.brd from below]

Board: 2 copper layers, 56.0 x 96.0 mm, 50 parts (13 on the bottom side), 61 nets.

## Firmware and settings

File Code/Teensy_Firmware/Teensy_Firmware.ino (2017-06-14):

#include "uLaren_CAN_Driver.h"
#include "FlexCAN.h"
#include "kinetis_flexcan.h"
#include "input_handler.h"
#include "output_handler.h"
#include "loop.h"
#include "fault_handler.h"
#include "structs.h"
#include "Adafruit_VL53L0X.h"

#define NODE_1 1
#define NODE_2 2
#define NODE_3 3
#define NODE_4 4

#define MC_VOLTAGE_THRESHOLD 220

#define SIMULINK 1

//main globals
FlexCAN CANbus(1000000);
State next_state;

//Laser Sensor
Adafruit_VL53L0X lox = Adafruit_VL53L0X();
VL53L0X_RangingMeasurementData_t measure;

//other data globals
// throttle input value (ranges from ~-500 to 500)
volatile int16_t THR_in;
//steering input value (ranges from ~-500 to 500)
volatile int16_t ST_in;
// URF measured distance, in mm (ranges from ~0-5000)
uint16_t URF_dist;
// IMU structure
extern IMUstruct IMUdat;

// Output variables 
long g1 = 0;
long g2 = 0;
long g3 = 0;
  imu::Vector<3> gyro1;   // Stores the 16-bit signed gyro sensor output
int16_t servo_out = 0;
int16_t throttle_out = 0;
int16_t throttle_out_LF = 0;
int16_t throttle_out_RF = 0;
int16_t throttle_out_LR = 0;
int16_t throttle_out_RR = 0;

//timing variables
unsigned long start_time_motors;
unsigned long current_time_motors;
unsigned long start_time_servo;
unsigned long current_time_servo;
unsigned long start_time_voltage;
unsigned long current_time_voltage;

//loop variables
int ret = 0;
int error = NO_ERROR;
int voltage = 0;
int data_int = 0;
/*********************************/
/*********   NOTES **************/
/*
 * ERROR_CAN_WRITE: a write to can error usually means one controller is offline.
 *        In this scenario we will go to INITIALIZE_CONTROLLERS and try to reboot them
 */
 
void setup() {
  //begin serial port operation
  Serial.begin(115200);
  if (SIMULINK)
  {
    Serial1.begin(115200);
    pinMode(PI_GPIO, OUTPUT);
    delay(10);
    digitalWrite(PI_GPIO, LOW);
  }
  //startup CAN network
  CANbus.begin();
  next_state = INITIALIZE_PERIPHERALS;
  indicatorSet(rgbWHITE);
}

void loop() {
  CAN_message_t msg;
  
   switch(next_state)
   {
      case(INITIALIZE_PERIPHERALS):
         //initialize other things
         if (PRINT) 
         {
          Serial.println("Initializing Peripherals");
         }
         initPWMin();
         initServo();
         if (!lox.begin())
         {
            //error state
            indicatorSet(rgbPURPLE);
            while(1);
         }
         next_state = INITIALIZE_CONTROLLERS;
         break;
      case(INITIALIZE_CONTROLLERS):
         if (PRINT)
         {
           Serial.println("Initializing Controllers");
         }
         ret = reset_nodes();
         if (ret > 0)
         {
          error = ret;
         }
         delay(1000);
         
         ret = initialize_CAN();
         if (ret > 0)
         {
          error = ret;
         }
         delay(50);
         
         ret = initialize_MC(NODE_1);
         if (ret > 0)
         {
          error = ret;
         }
         
         process_available_msgs();
         delay(100);
         ret = initialize_MC(NODE_2);
         if (ret > 0)
         {
          error = ret;
         }
         
         process_available_msgs();
         delay(100);
         ret = initialize_MC(NODE_3);
         if (ret > 0)
         {
          error = ret;
         }
         
         process_available_msgs();
         delay(100);
         ret = initialize_MC(NODE_4);
         if (ret > 0)
         {
          error = ret;
         }
        
         if (error == ERROR_CAN_WRITE)
         {
            //reinitialize controllers
            if (PRINT)
            {
              Serial.println("Stopping Nodes.");
            }
            
            delay(500);
            stop_remote_node(NODE_1);
            stop_remote_node(NODE_2);
            stop_remote_node(NODE_3);
            stop_remote_node(NODE_4);
            delay(500);
            process_available_msgs();
            if (PRINT)
            {
              Serial.println("Reinitializing Controllers.");
            }
            
            next_state = INITIALIZE_CONTROLLERS;
            error = 0;
         }
         else 
         {
            next_state = WAIT_FOR_ARM;
            indicatorSet(rgbYELLOW);
         }
         break;
      case(WAIT_FOR_ARM):
         if (PRINT)
         {
           Serial.println("Awaiting arming sequence... ");
         }
         
         while (ST_in < 400)
         {
            //do nothing until armed
            if (PRINT)
            {
              Serial.println(ST_in);
            }
            
            delay(500);
         }
         
         if (ST_in >= 400)
         {
            next_state = LINK_COMMUNICATION;
            indicatorSet(rgbRED);
         }
         else
         {
            next_state = WAIT_FOR_ARM;
         }
         
         break;
      case(LINK_COMMUNICATION):
          //arm
          link_node(NODE_1);
          delay(500);
          link_node(NODE_2);
          delay(500);
          link_node(NODE_3);
          delay(500);
          link_node(NODE_4);
          delay(500);

          if (SIMULINK)
          {
            next_state = RUNNING_SIMULINK;
            //write simulink pin high (pin 15) (PI_GPIO)
            digitalWrite(PI_GPIO, HIGH);
            indicatorSet(rgbCYAN);
          }
          else{
            next_state = RUNNING_NOMINALLY;
            indicatorSet(rgbGREEN);
          } 
            
           start_time_motors = micros();
           start_time_servo = micros();
           start_time_voltage = millis();
           if (PRINT)
           {
             Serial.println("Running under normal operations.");
           }  
          break;
      case(RUNNING_NOMINALLY):
          //check for messages
          while (CANbus.available())
          {
            if (CANbus.read(msg) != 0)
            {
              //Serial.println("ello matey");
              print_incoming_CAN_message(msg);
            }
          }

          //write to motor controllers
          current_time_motors = micros(); 
          if ((current_time_motors - start_time_motors) >= 20000)  //20ms => 50hz
          {
            start_time_motors = micros();
              
            write_velocity_and_enable_MC(NODE_1, -THR_in * SCALE_FACTOR);
            write_velocity_and_enable_MC(NODE_2, THR_in * SCALE_FACTOR);
            write_velocity_and_enable_MC(NODE_3, THR_in * SCALE_FACTOR);
            write_velocity_and_enable_MC(NODE_4, -THR_in * SCALE_FACTOR);
            
          }  

          //check voltage level
          current_time_voltage = millis();
          if ((current_time_voltage - start_time_voltage) >= 800)
          {
            voltage = query_voltage_level(NODE_1);
            start_time_voltage = millis();
            
             if (voltage < MC_VOLTAGE_THRESHOLD)
             {
                Serial.println("Voltage to motors is below our threshold. System is shutting down. Charge your battery!");
                //shutdown drivers 
                shutdown_MC(NODE_1);
                shutdown_MC(NODE_2);
                shutdown_MC(NODE_3);
                shutdown_MC(NODE_4);
                
                //make LED purple
                indicatorSet(rgbPURPLE);
                while(1);
             }
             indicatorSet(rgbGREEN);
          }

        
          // Push Actuator Data---------------------------------------
          // Set steering angle
          current_time_servo = micros();
          if ((current_time_servo - start_time_servo) >= 10000)
          {
            start_time_servo = micros();
            writeServo(ST_in);
          }
          
         break;
      case(RUNNING_SIMULINK):
          //check for CAN messages
          while (CANbus.available())
          {
            if (CANbus.read(msg) != 0)
            {
              //Serial.println("ello matey");
              print_incoming_CAN_message(msg);
            }
          }

          //write to motor controllers if we need to (50Hz)
          current_time_motors = micros(); 
          if ((current_time_motors - start_time_motors) >= 20000)  //20ms => 50hz
          {
            start_time_motors = micros();

            lox.rangingTest(&measure, false);
              
            write_velocity_and_enable_MC(NODE_1, -throttle_out_RF * SCALE_FACTOR);
            write_velocity_and_enable_MC(NODE_2, throttle_out_LF * SCALE_FACTOR);
            write_velocity_and_enable_MC(NODE_3, throttle_out_LR * SCALE_FACTOR);
            write_velocity_and_enable_MC(NODE_4, -throttle_out_RR * SCALE_FACTOR);
            Serial.println("I wrote to motors!");
          }   

          //process serial data (simulink) (simulink running at appx. 50Hz)
          while (Serial1.available() > 0)
          {
            data_int = Serial1.read();
            Serial.println(data_int);
            switch(data_int) 
            {
              case 11: //servo read from pi
                while (!Serial1.available())
                {
                  ;
                }
                servo_out = Serial1.read();
                while (!Serial1.available())
                {
                  ;
                }
                servo_out |= (Serial1.read()  << 8);
                break;
              case 12: //throttle RF read from pi
                while (!Serial1.available())
                {
                  ;
                }
                throttle_out_RF = Serial1.read();
                while (!Serial1.available())
                {
                  ;
                }
                throttle_out_RF |= (Serial1.read()  << 8);
                break;
              case 13: //throttle LF read from pi
              while (!Serial1.available())
                {
                  ;
                }
                throttle_out_LF = Serial1.read();
                while (!Serial1.available())
                {
                  ;
                }
                throttle_out_LF |= (Serial1.read()  << 8);
                break;
              case 14: //throttle LR read from pi
              while (!Serial1.available())
                {
                  ;
                }
                throttle_out_LR = Serial1.read();
                while (!Serial1.available())
                {
                  ;
                }
                throttle_out_LR |= (Serial1.read()  << 8);
                break;
              case 15: //throttle RR read from pi
                while (!Serial1.available())
                {
                  ;
                }
                throttle_out_RR = Serial1.read();
                while (!Serial1.available())
                {
                  ;
                }
                throttle_out_RR |= (Serial1.read()  << 8);
                break;
              case 21:  //servo write to pi
                if (PRINT)
                {
                  Serial.println(ST_in);
                }
                Serial1.write((const uint8_t*)&ST_in, 2);
                break;
              case 22:  //URF write to pi
                Serial1.write((const uint8_t*)&URF_dist, 2);
                break;
              case 23:  //gyroX write to pi
                Serial1.write((const uint8_t*)&g2, 2);
                break;
              case 24:  //gyroY write to pi
                Serial1.write((const uint8_t*)&g3, 2);
                break;
              case 25:  //gyroZ write to pi
                Serial1.write((const uint8_t*)&g1, 2);
                break;
              case 26:  //throttle write to pi
                if (PRINT)
                {
                  Serial.println(THR_in);
                }
                Serial1.write((const uint8_t*)&THR_in, 2);
                break;
              case 27:  //laser write to pi
                Serial1.write((const uint8_t*)&measure.RangeMilliMeter, 2);
                break;
             default:
                Serial.print("In Default case. Should NOT BE HERE. **");
                Serial.println(data_int);
                break;
            }
          }

          //check voltage level (1Hz)
          current_time_voltage = millis();
          if ((current_time_voltage - start_time_voltage) >= 1000)
          {
            voltage = query_voltage_level(NODE_1);
            start_time_voltage = millis();
            
             if (voltage < MC_VOLTAGE_THRESHOLD)
             {
                Serial.println("Voltage to motors is below our threshold. System is shutting down. Charge your battery!");
                //shutdown drivers 
                shutdown_MC(NODE_1);
                shutdown_MC(NODE_2);
                shutdown_MC(NODE_3);
                shutdown_MC(NODE_4);
                
                //make LED purple
                indicatorSet(rgbPURPLE);
             }
             indicatorSet(rgbCYAN);
          }

        
          // Push Actuator Data---------------------------------------
          // Set steering angle (100Hz)
          current_time_servo = micros();
          if ((current_time_servo - start_time_servo) >= 10000)
          {
            start_time_servo = micros();
            writeServo(servo_out);
          }
          
         break;
      case(INDICATE_AND_LOG_ERROR):
         if (PRINT)
         {
           Serial.println("Indicating and logging error.");
         }
         
         next_state = WAIT_FOR_CLEAR;
         break;
      case(WAIT_FOR_CLEAR):  
         delay(1000);
         next_state = WAIT_FOR_ARM;
         break;
      default:
         if (PRINT)
         {
          Serial.println("In default case. Should not be here. Ever.");
          Serial.print("Current state is: ");
          Serial.println(next_state);
         }
         
         exit(0);
         break;  
   }

}

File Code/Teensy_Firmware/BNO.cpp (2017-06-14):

/* 
 *  This .cpp file defines the content of functions to be called by the main routine
 */

// Allow access to arduino specific datatypes 
#include <arduino.h>
#include <Wire.h>
#include "Adafruit_Sensor.h"
#include "Adafruit_BNO055.h"
#include "imumaths.h"
#include "BNO.h"

// Define variables and constants. Voltatile is used for variables that are only modified in ISRs
// as the compiler is liable to treat them as constants.

// IMU---------------------------------- 

Adafruit_BNO055 bno = Adafruit_BNO055();


// Function output
IMUstruct IMUdat;
//--------------------------------------------------------

// Functions to initialize and utilize IMU comms-------------------------------------------------------------------------------
// communication functions

// initialize IMU
void initIMU(){
  delay(1000);
  Serial.println("Starting IMU");
  if(!bno.begin())
  {
    /* There was a problem  the BNO055 ... check your connections */
    Serial.println("No BNO055 detected");
    IMUdat.err = 1;
  }
  
  bno.setExtCrystalUse(true);
  delay(1000);
  Serial.println("BNO ready");
}

IMUstruct pollIMU(void){
  IMUdat.accel = bno.getVector(Adafruit_BNO055::VECTOR_ACCELEROMETER);
  IMUdat.gyro = bno.getVector(Adafruit_BNO055::VECTOR_GYROSCOPE);
  IMUdat.quat = bno.getQuat();
  IMUdat.mag = bno.getVector(Adafruit_BNO055::VECTOR_MAGNETOMETER);
  IMUdat.eul = bno.getVector(Adafruit_BNO055::VECTOR_EULER);
  IMUdat.lia = bno.getVector(Adafruit_BNO055::VECTOR_LINEARACCEL);
  IMUdat.grv = bno.getVector(Adafruit_BNO055::VECTOR_GRAVITY);
  return IMUdat;
}
//-------------------------------------------------------------------------------------------------------------------------------

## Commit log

2017-06-13 Added motherboard files
    [Motherboard.brd, Motherboard.sch]
2017-06-14 Added measured stock parts
    [A-Arm Dowel Pin.SLDPRT, Battery Cage.SLDPRT, Center Fixture_Rear.SLDPRT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]
2017-06-14 Custom 3d parts
    [222A - FRONT RIGHT MOTOR HOUSING.SLDDRW, Battery Bracket Small.SLDPRT, Battery bracket.SLDPRT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]
2017-06-14 Added rest of parts
    [20MM M4 Hex Standoff .SLDPRT, 25MM M4 Hex Standoff.SLDPRT, 40 MM M3 Standoff.SLDPRT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]
2017-06-15 Automation Files
    [Chassis Mounts.dxf, Chassis(in).DXF, FB(in).DXF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]

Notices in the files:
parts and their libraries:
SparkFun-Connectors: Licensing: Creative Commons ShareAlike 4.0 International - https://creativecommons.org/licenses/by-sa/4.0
